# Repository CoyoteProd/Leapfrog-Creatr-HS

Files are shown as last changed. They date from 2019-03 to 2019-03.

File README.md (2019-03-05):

# Leapfrog-Creatr-HS

Latest Marlin firmware for Leapfrog Creatr Hs based on Marlin 1.1.9

100% Compatible with the original mainboard

### WARNING ! 	
These releases seems to break communication with the display (Olimex A20). 

( Probably because by defaut Creatr HS use Checksumed Protocol ? )
### WARNING ! 	

## Marlin Std:
 - Acceleration and Feedrate diminued to have correct Print.
 - Linear Advance activated with Coef : 1.00

## Marlin BLTouch (same Standard settings)
- Add BLTouch

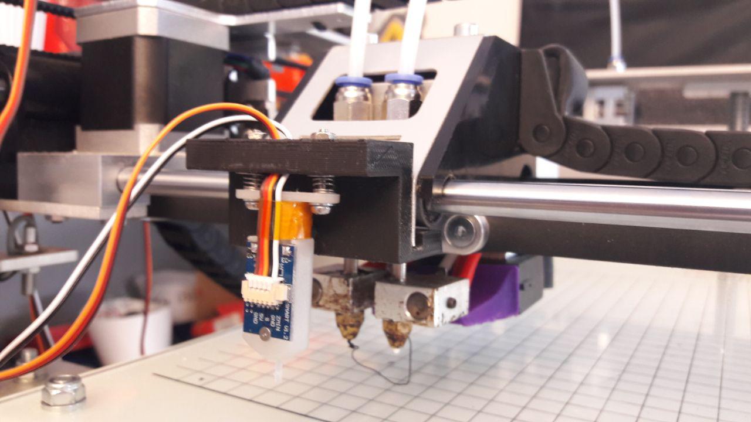
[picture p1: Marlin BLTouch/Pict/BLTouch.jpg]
BLTouch img

 
 - Connect Z (Black/White) on Zmin connector
 - Connect SERVO0_PIN on 52 (SCK) (physical pin 20 of ATMega2560) (see picture https://github.com/CoyoteProd/Leapfrog-Creatr-HS/blob/master/Marlin%20BLTouch/Pict/Servo.jpg )

Once installed, use this sequence to determine if the BLTouch is setup properly :

    Connect BLTouch, power up controller and upload the firmware
    
    LED will be ON if a servo signal is present.
    
    M119		; should return OPEN. If not check that the BLTouch is enabled in the configuration. If enabled then check wiring and Check that the correct pin is being used. Also check that Z_MIN_ENDSTOP_INVERTING and Z_MIN_PROBE_ENDSTOP_INVERTING are both set to "false".
    
    M280 P0 S10 	; should deploy the probe and the orange LED will be OFF.
    
    M119 		; should return OPEN
    
    M280 P0 S90 	; should stow the probe and the orange LED will be ON
    
    M280 P0 S60 	; puts it into the M119 test mode.
    		; The probe should remain stowed and the blue LED should be OFF. If it's ON then the unit needs to be adjusted.
    
    M119 		; should return TRIGGERED
    
    M280 P0 S160 	; returns it to normal operation
    
    M119 		; should return OPEN.
    
After that, Lower the bed to max, and initiate a Z Home (G28 Z) with a finger on the power supply (Safety first)
During Homing with other finger trigg bltouch: the bed must stop...( if not poweroff before crash....)

Future update : 
 
 - New Display interface for Olimex A20
 - (Add 200v Heated Bed with SSR)
 - (Change Nozzles by Volcano E3D)
 
Forked from : https://github.com/ledfreak3d/Leapfrog-Creatr-HS-New-Firmware

Original Firmware : https://github.com/Leapfrog3DPrinters/CreatrHS_Firmware_2.5

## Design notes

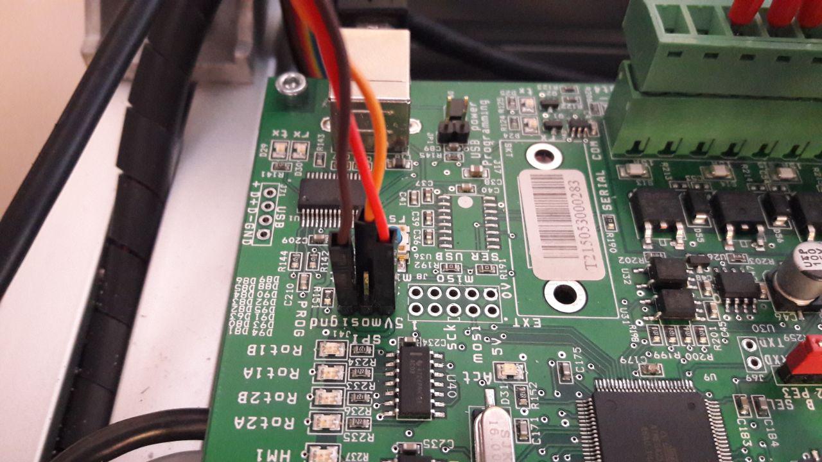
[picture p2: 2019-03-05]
Marlin BLTouch/Pict/Servo.jpg

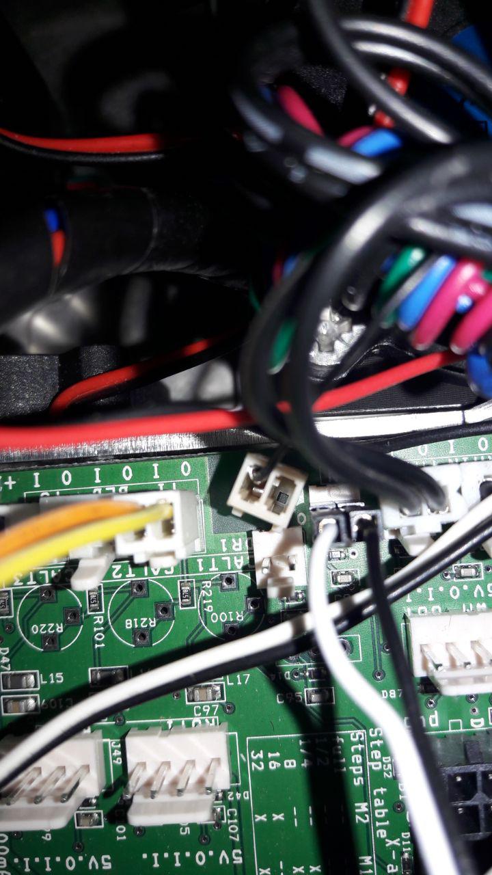
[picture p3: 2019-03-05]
Marlin BLTouch/Pict/Z-limit.jpg

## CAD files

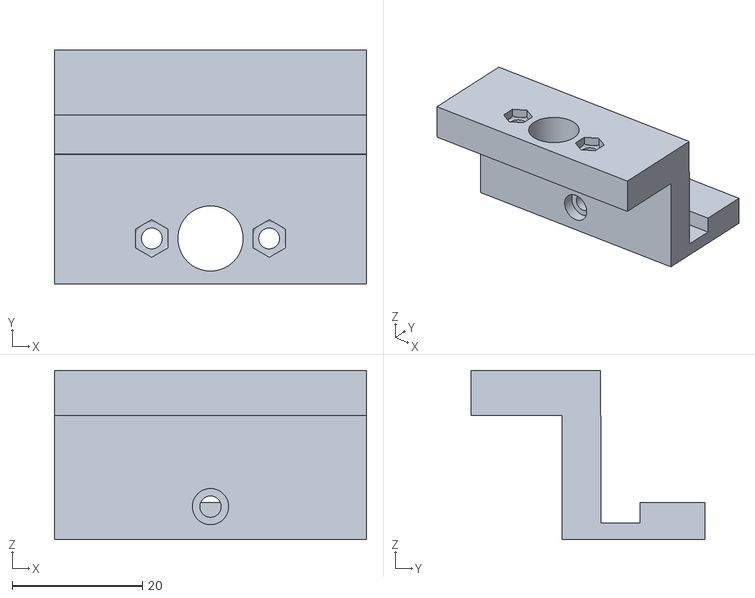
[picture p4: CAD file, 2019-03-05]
Marlin BLTouch/Support/support BLTouch.stl
47.9 x 35.9 x 26.0

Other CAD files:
Marlin BLTouch/Support/Support BLTouch v5.step

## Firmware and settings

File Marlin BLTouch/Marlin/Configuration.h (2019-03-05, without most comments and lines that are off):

#define CONFIGURATION_H
#define CONFIGURATION_H_VERSION 010109
#define STRING_CONFIG_H_AUTHOR "(Coyote Prod.)" // Who made the changes.
#define SHOW_BOOTSCREEN
#define STRING_SPLASH_LINE1 SHORT_BUILD_VERSION // will be shown during bootup in line 1
#define STRING_SPLASH_LINE2 WEBSITE_URL         // will be shown during bootup in line 2
#define SERIAL_PORT 0
#define BAUDRATE 250000
  #define MOTHERBOARD  BOARD_LEAPFROG
#define CUSTOM_MACHINE_NAME "Leapfrog Creatr HS"
#define EXTRUDERS 2
#define DEFAULT_NOMINAL_FILAMENT_DIA 1.75
#define HOTEND_OFFSET_X {0.0, -15.00} // (in mm) for each extruder, offset of the hotend on the X axis
#define HOTEND_OFFSET_Y {0.0, 0.00}  // (in mm) for each extruder, offset of the hotend on the Y axis
#define POWER_SUPPLY 0
#define TEMP_SENSOR_0 1
#define TEMP_SENSOR_1 1
#define TEMP_SENSOR_2 0
#define TEMP_SENSOR_BED 1
#define TEMP_RESIDENCY_TIME 10  // (seconds)
#define TEMP_HYSTERESIS 3       // (degC) range of +/- temperatures considered "close" to the target one
#define TEMP_WINDOW     1       // (degC) Window around target to start the residency timer x degC early.
#define TEMP_BED_RESIDENCY_TIME 10  // (seconds)
#define TEMP_BED_HYSTERESIS 3       // (degC) range of +/- temperatures considered "close" to the target one
#define TEMP_BED_WINDOW     1       // (degC) Window around target to start the residency timer x degC early.
#define HEATER_0_MINTEMP 5
#define HEATER_1_MINTEMP 5
#define HEATER_2_MINTEMP 5
#define HEATER_3_MINTEMP 5
#define HEATER_4_MINTEMP 5
#define BED_MINTEMP 5
#define HEATER_0_MAXTEMP 275
#define HEATER_1_MAXTEMP 275
#define HEATER_2_MAXTEMP 275
#define BED_MAXTEMP 100
#define PIDTEMP
#define BANG_MAX 255     // Limits current to nozzle while in bang-bang mode; 255=full current
#define PID_MAX BANG_MAX // Limits current to nozzle while PID is active (see PID_FUNCTIONAL_RANGE below); 255=full current
#define PID_K1 0.95      // Smoothing factor within any PID loop
  #define PID_FUNCTIONAL_RANGE 10 // If the temperature difference between the target temperature and the actual temperature
#define  DEFAULT_Kp 11.07
#define  DEFAULT_Ki 0.44
#define  DEFAULT_Kd 49.82
#define MAX_BED_POWER 255 // limits duty cycle to bed; 255=full current
#define PREVENT_COLD_EXTRUSION
#define EXTRUDE_MINTEMP 170
#define PREVENT_LENGTHY_EXTRUDE
#define EXTRUDE_MAXLENGTH 200
#define THERMAL_PROTECTION_HOTENDS // Enable thermal protection for all extruders
#define THERMAL_PROTECTION_BED     // Enable thermal protection for the heated bed
#define USE_XMIN_PLUG
#define USE_YMIN_PLUG
#define USE_ZMIN_PLUG
#define ENDSTOPPULLUPS
#define ENDSTOPPULLUP_ZMIN
#define X_MIN_ENDSTOP_INVERTING false // set to true to invert the logic of the endstop.
#define Y_MIN_ENDSTOP_INVERTING false // set to true to invert the logic of the endstop.
#define Z_MIN_ENDSTOP_INVERTING false // set to true to invert the logic of the endstop.
#define X_MAX_ENDSTOP_INVERTING false // set to true to invert the logic of the endstop.
#define Y_MAX_ENDSTOP_INVERTING false // set to true to invert the logic of the endstop.
#define Z_MAX_ENDSTOP_INVERTING false // set to true to invert the logic of the endstop.
#define Z_MIN_PROBE_ENDSTOP_INVERTING false // set to true to invert the logic of the probe.
#define X_DRIVER_TYPE  DRV8825
#define Y_DRIVER_TYPE  DRV8825
#define Z_DRIVER_TYPE  DRV8825
#define X2_DRIVER_TYPE DRV8825
#define Y2_DRIVER_TYPE DRV8825
#define Z2_DRIVER_TYPE DRV8825
#define E0_DRIVER_TYPE DRV8825
#define E1_DRIVER_TYPE DRV8825
#define DEFAULT_AXIS_STEPS_PER_UNIT   {(100.0/3)*2, (100.0/3)*2, 9600.0/10, 99.30}
#define DEFAULT_MAX_FEEDRATE          {300, 300, 30, 400}
#define DEFAULT_MAX_ACCELERATION      {3000,3000,100, 10000}
#define DEFAULT_ACCELERATION          2000    // X, Y, Z and E acceleration for printing moves
#define DEFAULT_RETRACT_ACCELERATION  3000    // E acceleration for retracts
#define DEFAULT_TRAVEL_ACCELERATION   2000    // X, Y, Z acceleration for travel (non printing) moves
#define DEFAULT_XJERK                 10.0
#define DEFAULT_YJERK                 10.0
#define DEFAULT_ZJERK                  0.4
#define DEFAULT_EJERK                  4.0
#define S_CURVE_ACCELERATION
#define Z_MIN_PROBE_USES_Z_MIN_ENDSTOP_PIN
#define BLTOUCH
  #define BLTOUCH_DELAY 100   // (ms) Enable and increase if needed
#define PROBING_HEATERS_OFF       // Turn heaters off when probing
#define PROBING_FANS_OFF          // Turn fans off when probing
#define X_PROBE_OFFSET_FROM_EXTRUDER   7      // X offset: -left  +right  [of the nozzle]
#define Y_PROBE_OFFSET_FROM_EXTRUDER -41      // Y offset: -front +behind [the nozzle]
#define Z_PROBE_OFFSET_FROM_EXTRUDER  -2.55   // Z offset: -below +above  [the nozzle]
#define MIN_PROBE_EDGE 10
#define XY_PROBE_SPEED 8000
#define Z_PROBE_SPEED_FAST HOMING_FEEDRATE_Z
#define Z_PROBE_SPEED_SLOW (Z_PROBE_SPEED_FAST / 2)
#define MULTIPLE_PROBING 2
#define Z_CLEARANCE_DEPLOY_PROBE   15 // Z Clearance for Deploy/Stow
#define Z_CLEARANCE_BETWEEN_PROBES  10 // Z Clearance between probe points
#define Z_CLEARANCE_MULTI_PROBE     5 // Z Clearance between multiple probes
#define Z_PROBE_LOW_POINT          -2 // Farthest distance below the trigger-point to go before stopping
#define Z_PROBE_OFFSET_RANGE_MIN -20
#define Z_PROBE_OFFSET_RANGE_MAX 20
#define X_ENABLE_ON 0
#define Y_ENABLE_ON 0
#define Z_ENABLE_ON 0
#define E_ENABLE_ON 0 // For all extruders
#define DISABLE_X false
#define DISABLE_Y false
#define DISABLE_Z false
#define DISABLE_E false // For all extruders
#define DISABLE_INACTIVE_EXTRUDER true // Keep only the active extruder enabled.
#define INVERT_X_DIR false
#define INVERT_Y_DIR false
#define INVERT_Z_DIR true
#define INVERT_E0_DIR false
#define INVERT_E1_DIR true
#define INVERT_E2_DIR true
#define INVERT_E3_DIR false
#define INVERT_E4_DIR false
#define X_HOME_DIR -1
#define Y_HOME_DIR -1
#define Z_HOME_DIR -1
#define X_BED_SIZE 270
#define Y_BED_SIZE 280
#define X_MIN_POS 0
#define Y_MIN_POS 0
#define Z_MIN_POS 0
#define X_MAX_POS X_BED_SIZE
#define Y_MAX_POS Y_BED_SIZE
#define Z_MAX_POS 180
#define MIN_SOFTWARE_ENDSTOPS
  #define MIN_SOFTWARE_ENDSTOP_X
  #define MIN_SOFTWARE_ENDSTOP_Y
  #define MIN_SOFTWARE_ENDSTOP_Z
#define MAX_SOFTWARE_ENDSTOPS
  #define MAX_SOFTWARE_ENDSTOP_X
  #define MAX_SOFTWARE_ENDSTOP_Y
  #define MAX_SOFTWARE_ENDSTOP_Z
#define AUTO_BED_LEVELING_BILINEAR
  #define ENABLE_LEVELING_FADE_HEIGHT
  #define SEGMENT_LEVELED_MOVES
  #define LEVELED_SEGMENT_LENGTH 5.0 // (mm) Length of all segments (except the last one)
  #define GRID_MAX_POINTS_X 4
  #define GRID_MAX_POINTS_Y GRID_MAX_POINTS_X
#define Z_SAFE_HOMING
  #define Z_SAFE_HOMING_X_POINT ((X_BED_SIZE) / 2)    // X point for Z homing when homing all axes (G28).
  #define Z_SAFE_HOMING_Y_POINT ((Y_BED_SIZE) / 2)    // Y point for Z homing when homing all axes (G28).
#define HOMING_FEEDRATE_XY (70*60)
#define HOMING_FEEDRATE_Z  (20*60)
#define EEPROM_SETTINGS // Enable for M500 and M501 commands
#define EEPROM_CHITCHAT   // Give feedback on EEPROM commands. Disable to save PROGMEM.
#define HOST_KEEPALIVE_FEATURE        // Disable this if your host doesn't like keepalive messages
#define DEFAULT_KEEPALIVE_INTERVAL 2  // Number of seconds between "busy" messages. Set with M113.
#define BUSY_WHILE_HEATING            // Some hosts require "busy" messages even during heating
#define PREHEAT_1_TEMP_HOTEND 200
#define PREHEAT_1_TEMP_BED     50
#define PREHEAT_1_FAN_SPEED     0 // Value from 0 to 255
#define PREHEAT_2_TEMP_HOTEND 240
#define PREHEAT_2_TEMP_BED    110
#define PREHEAT_2_FAN_SPEED     0 // Value from 0 to 255
#define PRINTJOB_TIMER_AUTOSTART
#define LCD_LANGUAGE en
#define DISPLAY_CHARSET_HD44780 JAPANESE
#define SOFT_PWM_SCALE 0
#define NUM_SERVOS 1 // Servo index starts with 0 for M280 command
#define SERVO_DELAY { 300 }

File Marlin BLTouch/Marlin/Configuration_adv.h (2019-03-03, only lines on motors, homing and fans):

#define E0_AUTO_FAN_PIN -1
#define E1_AUTO_FAN_PIN -1
#define E2_AUTO_FAN_PIN -1
#define E3_AUTO_FAN_PIN -1
#define E4_AUTO_FAN_PIN -1
#define CHAMBER_AUTO_FAN_PIN -1
#define X_HOME_BUMP_MM 5
#define Y_HOME_BUMP_MM 5
#define Z_HOME_BUMP_MM 2
#define HOMING_BUMP_DIVISOR { 2, 2, 4 }  // Re-Bump Speed Divisor (Divides the Homing Feedrate)
#define MICROSTEP_MODES { 16, 16, 16, 16, 16 } // [1,2,4,8,16]
#define DIGIPOT_I2C_MOTOR_CURRENTS { 1.0, 1.0, 1.0, 1.0, 1.0, 1.0, 1.0, 1.0 }  //  AZTEEG_X3_PRO
#define LIN_ADVANCE
  #define LIN_ADVANCE_K 1  // Unit: mm compression per 1mm/s extruder speed

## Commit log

2019-03-04 Add original Firmware
    [Configuration.h, Configuration_adv.h]
2019-03-05 Add BLTouch
    [Configuration.h, Configuration_adv.h, Support BLTouch v5.step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]

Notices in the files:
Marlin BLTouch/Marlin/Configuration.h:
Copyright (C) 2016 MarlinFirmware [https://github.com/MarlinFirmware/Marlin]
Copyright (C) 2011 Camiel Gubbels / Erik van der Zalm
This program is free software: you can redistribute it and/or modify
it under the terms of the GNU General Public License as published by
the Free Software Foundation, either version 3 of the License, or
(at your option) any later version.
